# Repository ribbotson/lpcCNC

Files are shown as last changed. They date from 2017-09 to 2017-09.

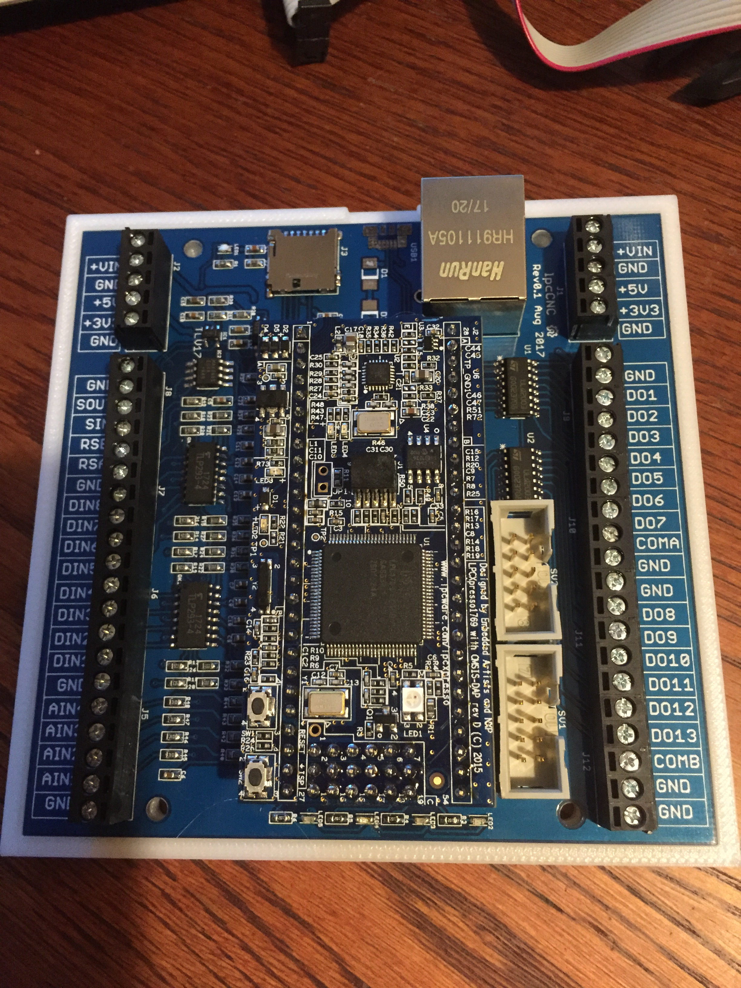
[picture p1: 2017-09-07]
document/IMG_2888.JPG

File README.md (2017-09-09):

# lpcCNC Smoothieboard Derivative for CNC applications

This free open source derivative of the Smoothieboard is designed for CNC applications. It is intended for use with external stepper motor drivers. It features 13 digital open collector outputs, 8 digital inputs, 4 analog inputs, RS485 interface for spindle, 10V analog output for spindle, support for LCD screen, Ethernet, and power supply up to 40V.

## Content

This is a hardware project with PCB design file in Eagle. A 3D printable case ([Top]( http://a360.co/2vPnznS), [Bottom](http://a360.co/2j534xu)) design in Fusion360 is also provided. Example configuration files for Smoothieware and grbl-lpc are also provided.

## Authors

* **Richard Ibbotson**  

## License

Licensed under CERN OHL v.1.2 or later https://www.ohwr.org/documents/294 No warranty is provided for this documentation implied or otherwise.

## Acknowledgments

* All the folks at [rLab](http://www.rlab.org.uk) Reading Hackspace especially Toby
+ The Smoothieboard creators and the [Smoothieware](http://smoothieware.org/) team

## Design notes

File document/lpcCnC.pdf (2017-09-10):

Lable | CPU Pin | Description
+VIN | N/A | External Power Supply input
GND | GND | System Ground
+5V | N/A | +5V Power Supply Output
+3V3 | N/A | +3V3 Power Supply Output
GND | GND | System Ground
SGND | N/A | Isolated Ground for Analog Spindle
SOUT | N/A | 0-> 10V Output for Analog Spindle
SIN | N/A | 10V supply in for Analog Spindle
RSB | N/A | - RS485 for Spindle
RSA | N/A | +RS485 for Spindle
GND | GND | System Ground
DIN8 | 2.13 | Digital Input
DIN7 | 1.31 | Digital Input
DIN6 | 1.29 | Digital Input
DIN5 | 1.28 | Digital Input
DIN4 | 1.26 | Digital Input
DIN3 | 1.25 | Digital Input
DIN2 | 1.24 | Digital Input
DIN1 | 1.23 | Digital Input
GND | GND | System Ground
AIN4 | 0.23 | Analog Input
AIN3 | 0.24 | Analog Input
AIN2 | 0.25 | Analog Input
AIN1 | 0.26 | Analog Input
GND | GND | System Ground

# lpcCNC Screw Terminal Mapping

Lable | CPU Pin | Description
+VIN | N/A | External Power Supply input
GND | GND | System Ground
+5V | N/A | +5V Power Supply Output
+3V3 | N/A | +3V3 Power Supply Output
GND | GND | System Ground
GND | GND | System Ground
DO1 | 0.4 | Digital Output
DO2 | 0.5 | Digital Output
DO3 | 0.10 | Digital Output
DO4 | 0.11 | Digital Output
DO5 | 2.0 | Digital Output
DO6 | 2.1 | Digital Output
DO7 | 2.2 | Digital Output
COMA | N/A | Protection Diode for DO1 to DO7
GND | GND | System Ground
GND | GND | System Ground
DO8 | 2.3 | Digital Output
DO9 | 2.4 | Digital Output
DO10 | 2.11 | Digital Output
DO11 | 2.8 | Digital Output
DO12 | 2.7 | Digital Output
DO13 | 2.6 | Digital Output
COMB | N/A | Protection Diode for DO8 to DO13
GND | GND | System Ground
GND | GND | System Ground

# lpcCNC CPU Pin Usage

Pin | Usage
0.0 | RS485 RX for Spindle
0.1 | RS485 TX for Spindle
0.2 | UART TX to LCD Panel and ISP AUX3 Pin 2
0.3 | UART RX to LCD Panel and ISP AUX3 Pin 1
0.4 | DO1 Digital Output
0.5 | DO2 Digital Output
0.6 | SSEL for Internal SD Card
0.7 | SCK for internal SD Card
0.8 | MISO for Internal SD Card
0.9 | MOSI for Internal SD Card
0.10 | DO3 Digital Output
0.11 | DO4 Digital Output
0.15 | SCK for LCD Panel AUX3 Pin 7
0.16 | SSEL for LCD Panel SD Card AUX3 Pin 8
0.17 | MOSI for LCD Panel AUX3 Pin6
0.18 | MISO for LCD Panel AUX3 Pin 5
0.19 | SDA Internal EEPROM
0.20 | SCL Internal EEPROM
0.21 | RS485 Direction for Spindle
0.22 | RED Diagnostic LED
0.23 | AN4 Analog Input
0.24 | AN3 Analog Input
0.25 | AN2 Analog Input
0.26 | AN1 Analog Input
0.27 | Not Used
0.28 | Not Used
0.29 | USB – Micro USB Connector
0.30 | USB + Micro USB Connector
Pin | Usage
1.0 | Ethernet
1.1 | Ethernet
1.4 | Ethernet
1.8 | Ethernet
1.9 | Ethernet
1.10 | Ethernet
1.14 | Ethernet
1.15 | Ethernet
1.16 | Ethernet
1.17 | Ethernet
1.18 | LED 2
1.19 | LED 3
1.20 | LED 4
1.21 | LED 5
1.22 | SSEL for LCD Panel LCD AUX2 Pin 3
1.23 | DIN1 Digital Input
1.24 | DIN2 Digital Input
1.25 | DIN3 Digital Input
1.26 | DIN4 Digital Input
1.27 | Encoder B for LC D Panel AUX 2 Pin 6
1.28 | DIN5 Digital Input
1.29 | DIN6 Digital Input
1.30 | Buzzer for LCD Panel AUX 2 Pin 2
1.31 | DIN7 Digital Input
Pin | Usage
2.0 | DO5 Digital Output
2.1 | DO6 Digital Output
2.2 | DO7 Digital Output
2.3 | DO8 Digital Output
2.4 | DO9 Digital Output
2.5 | PWM for Analog Spindle
2.6 | DO13 Digital Output
2.7 | DO12 Digital Output
2.8 | DO11 Digital Output
2.9 | USB Connect Internal
2.10 | ISP Enable Internal
2.11 | DO10 Digital Output
2.12 | A0 for LCD Panel AUX2 Pin 5
2.13 | DIN8 Digital Input
Pin | Usage
4.28 | Encoder Click for LCD Panel AUX2 Pin 1
4.29 | Encoder A for LCD Panel AUX2 Pin 8
Pin | Usage
3.25 | BLUE Diagnostic LED
3.26 | GREEN Diagnostic LED
Pin | Usage
Reset | Reset from LCD Panel AUX2 Pin 4

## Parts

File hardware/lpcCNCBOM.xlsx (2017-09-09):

Column1 | Column2 | Column3 | Column4 | Column5 | Column6 | Column7 | Column8 | Column9
Part | Value | Device | Package | Description | Manufacturer | Manufacturer Part Number | Supplier | Supplier Part number
AUX2 | 10 Way | Header | 10 Way | 10 Way Boxed Header | TruConnect | DS1013-10 | Rapid | 19-0033
AUX3 | 10 Way | Header | ML10 | 10 Way Boxed Header | TruConnect | DS1013-10 | Rapid | 19-0033
C1 | 100n | Cap Ceramic 50V | 0603 | Ceramic Capacitors | Murata | GRM188F51H104ZA01D | RS | 723-5534
C2 | 100n | Cap Ceramic 50V | 0603 | Ceramic Capacitors | Murata | GRM188F51H104ZA01D | RS | 723-5534
C3 | 100n | Cap Ceramic 50V | 0603 | Ceramic Capacitors | Murata | GRM188F51H104ZA01D | RS | 723-5534
C4 | 100n | Cap Ceramic 50V | 0603 | Ceramic Capacitors | Murata | GRM188F51H104ZA01D | RS | 723-5534
C5 | 100n | Cap Ceramic 50V | 0603 | Ceramic Capacitors | Murata | GRM188F51H104ZA01D | RS | 723-5534
C6 | 100n | Cap Ceramic 50V | 0603 | Ceramic Capacitors | Murata | GRM188F51H104ZA01D | RS | 723-5534
C7 | 100n | Cap Ceramic 50V | 0603 | Ceramic Capacitors | Murata | GRM188F51H104ZA01D | RS | 723-5534
C8 | 100n | Cap Ceramic 50V | 0603 | Ceramic Capacitors | Murata | GRM188F51H104ZA01D | RS | 723-5534
C9 | 100n | Cap Ceramic 50V | 0603 | Ceramic Capacitors | Murata | GRM188F51H104ZA01D | RS | 723-5534
C10 | 100n | Cap Ceramic 50V | 0603 | Ceramic Capacitors | Murata | GRM188F51H104ZA01D | RS | 723-5534
C11 | 100n | Cap Ceramic 50V | 0603 | Ceramic Capacitors | Murata | GRM188F51H104ZA01D | RS | 723-5534
C12 | 100n | Cap Ceramic 50V | 0603 | Ceramic Capacitors | Murata | GRM188F51H104ZA01D | RS | 723-5534
C13 | 100n | Cap Ceramic 50V | 0603 | Ceramic Capacitors | Murata | GRM188F51H104ZA01D | RS | 723-5534
C14 | 100n | Cap Ceramic 50V | 0603 | Ceramic Capacitors | Murata | GRM188F51H104ZA01D | RS | 723-5534
C15 | 47n | Cap Ceramic 50V | 0603 | Ceramic Capacitors | Murata | GRM188B11E473KA01D | RS | 798-0332
C16 | 1uF | Cap Ceramic 25V | 0603 | Ceramic Capacitors | Murata | GRM188R61E105KA12D | RS | 723-5587
C17 | 100n | Cap Ceramic 50V | 0603 | Ceramic Capacitors | Murata | GRM188F51H104ZA01D | RS | 723-5534
C18 | 100n | Cap Ceramic 50V | 0603 | Ceramic Capacitors | Murata | GRM188F51H104ZA01D | RS | 723-5534
C19 | 1uF | Cap Ceramic 25V | 0603 | Ceramic Capacitors | Murata | GRM188R61E105KA12D | RS | 723-5587
C20 | 1uF | Cap Ceramic 25V | 0603 | Ceramic Capacitors | Murata | GRM188R61E105KA12D | RS | 723-5587
C21 | 1uF | Cap Ceramic 25V | 0603 | Ceramic Capacitors | Murata | GRM188R61E105KA12D | RS | 723-5587
C22 | 1uF | Cap Ceramic 25V | 0603 | Ceramic Capacitors | Murata | GRM188R61E105KA12D | RS | 723-5587
C23 | 100n | Cap Ceramic 50V | 0603 | Ceramic Capacitors | Murata | GRM188F51H104ZA01D | RS | 723-5534
D1 | MBRA140 | DIODE-DO-214AC | DO-214AC | Schottky Power Diode | ON Semi | MBRA140T3G | RS | 625-5650
D2 | MBRA140 | DIODE-DO-214AC | DO-214AC | Schottky Power Diode | ON Semi | MBRA140T3G | RS | 625-5650
D3 | BAS70-04 | DIODE_2CACA-SOT23 | SOT23 | Dual Schottky Diode | Multicomp | BAS70-04 | Farnell | 179-7835
D4 | BAS70-04 | DIODE_2CACA-SOT23 | SOT23 | Dual Schottky Diode | Multicomp | BAS70-04 | Farnell | 179-7835
D5 | BAS70-04 | DIODE_2CACA-SOT23 | SOT23 | Dual Schottky Diode | Multicomp | BAS70-04 | Farnell | 179-7835
D6 | BAS70-04 | DIODE_2CACA-SOT23 | SOT23 | Dual Schottky Diode | Multicomp | BAS70-04 | Farnell | 179-7835
IC1 | TLV172 | TLV172MF | SOT23-5 | Low Power Single Op Amp | Texas Instruments | TLV172IDBVR | Farnell | 267-7088
IC2 | MAX3485 | MAX481CSA | SO08 | RS485 Transceiver | Maxim | MAX3485ECSA+ | Farnell | 251-8816
J1 | 1X5 | 1X5 | 1X05-3.5MM | 3.5mm Pitch Screw Header | CamdenBoss | CTB3051/5BK | Rapid | 21-4708
J2 | 1X5 | 1X5 | 1X05-3.5MM | 3.5mm Pitch Screw Header | CamdenBoss | CTB3051/5BK | Rapid | 21-4708
J3 |  | AMPHENOL_114-00841-68 | AMPHENOL_114-00841-68 | Micro SD Card Holder | Amphenol | 114-00841-68 | Farnell | 266-6772
J4 | HR911105A | HR911105A | HR911105A | Ethernet Mag Jack | HanRun | HR911105A | eBay | HR911105A
J5 | 1X5 | 1X5 | 1X05-3.5MM | 3.5mm Pitch Screw Header | CamdenBoss | CTB3051/5BK | Rapid | 21-4708
J6 | 1X5 | 1X5 | 1X05-3.5MM | 3.5mm Pitch Screw Header | CamdenBoss | CTB3051/5BK | Rapid | 21-4708
J7 | 1X5 | 1X5 | 1X05-3.5MM | 3.5mm Pitch Screw Header | CamdenBoss | CTB3051/5BK | Rapid | 21-4708
J8 | 1X5 | 1X5 | 1X05-3.5MM | 3.5mm Pitch Screw Header | CamdenBoss | CTB3051/5BK | Rapid | 21-4708
J9 | 1X5 | 1X5 | 1X05-3.5MM | 3.5mm Pitch Screw Header | CamdenBoss | CTB3051/5BK | Rapid | 21-4708
J10 | 1X5 | 1X5 | 1X05-3.5MM | 3.5mm Pitch Screw Header | CamdenBoss | CTB3051/5BK | Rapid | 21-4708
J11 | 1X5 | 1X5 | 1X05-3.5MM | 3.5mm Pitch Screw Header | CamdenBoss | CTB3051/5BK | Rapid | 21-4708
J12 | 1X5 | 1X5 | 1X05-3.5MM | 3.5mm Pitch Screw Header | CamdenBoss | CTB3051/5BK | Rapid | 21-4708
J13 | 27 pin | 2.54mm Pitch Female | Pin Header | Female Pin Header |  | 40 Pin strip | eBay
J14 | 27 pin | 2.54mm Pitch Female | Pin Header | Female Pin Header |  | 40 Pin strip | eBay
J15 | 4 pin | 2.54mm Pitch Female | Pin Header | Female Pin Header |  | 40 Pin strip | eBay
J16 | 3 pin | 2.54mm Pitch Female | Pin Header | Female Pin Header |  | 40 Pin strip | eBay
J17 | 3 pin | 2.54mm Pitch Female | Pin Header | Female Pin Header |  | 40 Pin strip | eBay
J18 | 3 pin | 2.54mm Pitch Female | Pin Header | Female Pin Header |  | 40 Pin strip | eBay
J19 | 27 pin | 2.54mm Pitch Male | Pin Header | Male Pin Header |  | 40 Pin strip | eBay
J20 | 27 pin | 2.54mm Pitch Male | Pin Header | Male Pin Header |  | 40 Pin strip | eBay
J21 | 4 pin | 2.54mm Pitch Male | Pin Header | Male Pin Header |  | 40 Pin strip | eBay
J22 | 3 pin | 2.54mm Pitch Male | Pin Header | Male Pin Header |  | 40 Pin strip | eBay
J23 | 3 pin | 2.54mm Pitch Male | Pin Header | Male Pin Header |  | 40 Pin strip | eBay
J24 | 3 pin | 2.54mm Pitch Male | Pin Header | Male Pin Header |  | 40 Pin strip | eBay
LED1 | Green |  | LED 0603 | SMT LED | Osram | LP L296-J2L2-25 | RS | 915-4768
LED2 | Green |  | LED 0603 | SMT LED | Osram | LP L296-J2L2-25 | RS | 915-4768
LED3 | Green |  | LED 0603 | SMT LED | Osram | LP L296-J2L2-25 | RS | 915-4768
LED4 | Green |  | LED 0603 | SMT LED | Osram | LP L296-J2L2-25 | RS | 915-4768
LED5 | Green |  | LED 0603 | SMT LED | Osram | LP L296-J2L2-25 | RS | 915-4768
LPC1 | LPC Expresso1769 | LPCXPRESSO_LPC1769 | Custom | Processor Module | NXP | OM13085UL | Farnell | 252-3091
OC1 | TLP293-4 | TLP293-4 | SOIC16 | Quad Optocoupler | Toshiba | TLP293-4 | Farnell | 252-4319
OC2 | TLP293-4 | TLP293-4 | SOIC16 | Quad Optocoupler | Toshiba | Toshiba | Farnell | 252-4319
OC3 | ACPL217-500E | ACPL217 | SOIC4 | Optocoupler | Avago | ACPL-217-500E | Rapid | 75-0230
R1 | 1K | RESISTOR0603 | 0603 | Resistors | Panasonic | ERJ3EKF1001V | RS | 873-9223
R2 | 100K | RESISTOR0603 | 0603 | Resistors | Panasonic | ERJU03F1003V | RS | 873-9220
R3 | 1K | RESISTOR0603 | 0603 | Resistors | Panasonic | ERJ3EKF1001V | RS | 873-9223
R4 | 1K | RESISTOR0603 | 0603 | Resistors | Panasonic | ERJ3EKF1001V | RS | 873-9223
R5 | 1K | RESISTOR0603 | 0603 | Resistors | Panasonic | ERJ3EKF1001V | RS | 873-9223
R6 | 1K | RESISTOR0603 | 0603 | Resistors | Panasonic | ERJ3EKF1001V | RS | 873-9223
R7 | Do Not Fit | RESISTOR0603 | 0603 | Resistors | Vishay | CRCW06030000Z0EB | RS | 678-9670
R8 | 0R | RESISTOR0603 | 0603 | Resistors | Vishay | CRCW06030000Z0EB | RS | 678-9670
R9 | Do Not Fit | RESISTOR0603 | 0603 | Resistors | Vishay | CRCW06030000Z0EB | RS | 678-9670
R10 | Do Not Fit | RESISTOR0603 | 0603 | Resistors | Vishay | CRCW06030000Z0EB | RS | 678-9670
R11 | 0R | RESISTOR0603 | 0603 | Resistors | Vishay | CRCW06030000Z0EB | RS | 678-9670
R12 | Do Not Fit | RESISTOR0603 | 0603 | Resistors | Vishay | CRCW06030000Z0EB | RS | 678-9670
R13 | 470R | RESISTOR0603 | 0603 | Resistors | Panasonic | ERJPA3F4700V | RS | 862-6966
R14 | 470R | RESISTOR0603 | 0603 | Resistors | Panasonic | ERJPA3F4700V | RS | 862-6966
R15 | 470R | RESISTOR0603 | 0603 | Resistors | Panasonic | ERJPA3F4700V | RS | 862-6966
R16 | 470R | RESISTOR0603 | 0603 | Resistors | Panasonic | ERJPA3F4700V | RS | 862-6966
R17 | 470R | RESISTOR0603 | 0603 | Resistors | Panasonic | ERJPA3F4700V | RS | 862-6966
R18 | 470R | RESISTOR0603 | 0603 | Resistors | Panasonic | ERJPA3F4700V | RS | 862-6966
R19 | 470R | RESISTOR0603 | 0603 | Resistors | Panasonic | ERJPA3F4700V | RS | 862-6966
R20 | 470R | RESISTOR0603 | 0603 | Resistors | Panasonic | ERJPA3F4700V | RS | 862-6966
R21 | 2K2 | RESISTOR0603 | 0603 | Resistors | Panasonic | ERJU03F2201V | RS | 213-2317
R22 | 2K2 | RESISTOR0603 | 0603 | Resistors | Panasonic | ERJU03F2201V | RS | 213-2317
R23 | 2K2 | RESISTOR0603 | 0603 | Resistors | Panasonic | ERJU03F2201V | RS | 213-2317
R24 | 2K2 | RESISTOR0603 | 0603 | Resistors | Panasonic | ERJU03F2201V | RS | 213-2317
R25 | 2K2 | RESISTOR0603 | 0603 | Resistors | Panasonic | ERJU03F2201V | RS | 213-2317
R26 | 2K2 | RESISTOR0603 | 0603 | Resistors | Panasonic | ERJU03F2201V | RS | 213-2317
R27 | 2K2 | RESISTOR0603 | 0603 | Resistors | Panasonic | ERJU03F2201V | RS | 213-2317
R28 | 2K2 | RESISTOR0603 | 0603 | Resistors | Panasonic | ERJU03F2201V | RS | 213-2317
R29 | 1K | RESISTOR0603 | 0603 | Resistors | Panasonic | ERJ3EKF1001V | RS | 873-9223
R30 | 1K | RESISTOR0603 | 0603 | Resistors | Panasonic | ERJ3EKF1001V | RS | 873-9223
R31 | 1K | RESISTOR0603 | 0603 | Resistors | Panasonic | ERJ3EKF1001V | RS | 873-9223
R32 | 1K | RESISTOR0603 | 0603 | Resistors | Panasonic | ERJ3EKF1001V | RS | 873-9223
R33 | 1K | RESISTOR0603 | 0603 | Resistors | Panasonic | ERJ3EKF1001V | RS | 873-9223
R34 | 1K | RESISTOR0603 | 0603 | Resistors | Panasonic | ERJ3EKF1001V | RS | 873-9223
R35 | 1K | RESISTOR0603 | 0603 | Resistors | Panasonic | ERJ3EKF1001V | RS | 873-9223
R36 | 1K | RESISTOR0603 | 0603 | Resistors | Panasonic | ERJ3EKF1001V | RS | 873-9223
R37 | 470R | RESISTOR0603 | 0603 | Resistors | Panasonic | ERJPA3F4700V | RS | 862-6966
R38 | 2K2 | RESISTOR0603 | 0603 | Resistors | Panasonic | ERJU03F2201V | RS | 213-2317
R39 | 47K | RESISTOR0603 | 0603 | Resistors | Panasonic | ERJU03F4702V | RS | 873-9490
R40 | 4K7 | RESISTOR0603 | 0603 | Resistors | Panasonic | ERJU03F4701V | RS | 873-9497
R41 | 100K | RESISTOR0603 | 0603 | Resistors | Panasonic | ERJU03F1003V | RS | 873-9220
R42 | 4K7 | RESISTOR0603 | 0603 | Resistors | Panasonic | ERJU03F4701V | RS | 873-9497
R43 | 4K7 | RESISTOR0603 | 0603 | Resistors | Panasonic | ERJU03F4701V | RS | 873-9497
R44 | 4K7 | RESISTOR0603 | 0603 | Resistors | Panasonic | ERJU03F4701V | RS | 873-9497
R45 | 10K | RESISTOR0603 | 0603 | Resistors | Panasonic | ERJU03F1002V | RS | 873-9226
R46 | 10K | RESISTOR0603 | 0603 | Resistors | Panasonic | ERJU03F1002V | RS | 873-9226
R47 | 10K | RESISTOR0603 | 0603 | Resistors | Panasonic | ERJU03F1002V | RS | 873-9226
R48 | 10K | RESISTOR0603 | 0603 | Resistors | Panasonic | ERJU03F1002V | RS | 873-9226
R49 | 120R | RESISTOR0603 | 0603 | Resistors | Panasonic | ERJU03F1200V | RS | 873-9254
U1 | ULQ2003 | ULQ2003 | SOIC16 | DARLINGTON TRANSISTOR ARRAYS | ST Micro | ULQ2003D1013TR | Farnell | 234-1742
U2 | ULQ2003 | ULQ2003 | SOIC16 | DARLINGTON TRANSISTOR ARRAYS | ST Micro | ULQ2003D1013TR | Farnell | 234-1742
USB1 | MOLEX-47346-0001 | MOLEX-47346-0001 | MOLEX-47364-0001 | Micro USB Connector SMT | Molex | 47364-001 | RS | 702-5475
VR1 | 78SR | 78SR | Custom | 5V Switching DC DC non isolated converter | Murata | OKI-78SR-5/1.5-W36H-C | RS | 796-2138
PCB |  |  | Custom | Printed Circuit Board 2 Layer | PCB | Github File | PCBWay | Github File
Case Lid |  |  | Custom | ABS 3D Print | 3D Printed | Github File | 3D Hubs | Github File
Case Base |  |  | Custom | ABS 3D Print | 3D Printed | Github File | 3D Hubs | Github File
SC1 | CSK Self tapping | 2.2mm * 13mm |  | Self Tapping Countersink screw |  |  | eBay
SC2 | CSK Self tapping | 2.2mm * 13mm |  | Self Tapping Countersink screw |  |  | eBay
SC3 | CSK Self tapping | 2.2mm * 13mm |  | Self Tapping Countersink screw |  |  | eBay
SC4 | CSK Self tapping | 2.2mm * 13mm |  | Self Tapping Countersink screw |  |  | eBay
SD1 | 4Gb Micro SD |  |  | Micro SD Card
LCD1 | LCD Panel |  |  | AZS MZ LCD Display inc cables |  |  | Aliexpress

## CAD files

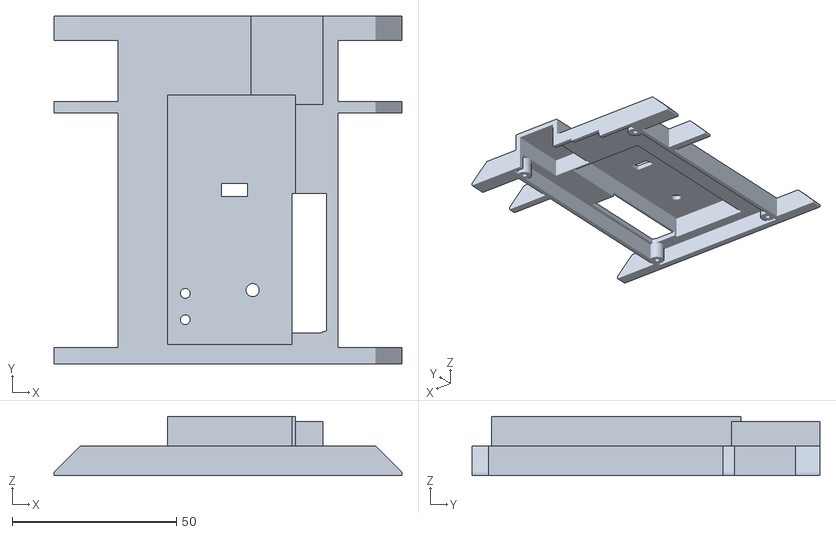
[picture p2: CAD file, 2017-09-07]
hardware/Case/STL/lpcCNC_Lid v15.stl
106.0 x 106.0 x 18.0

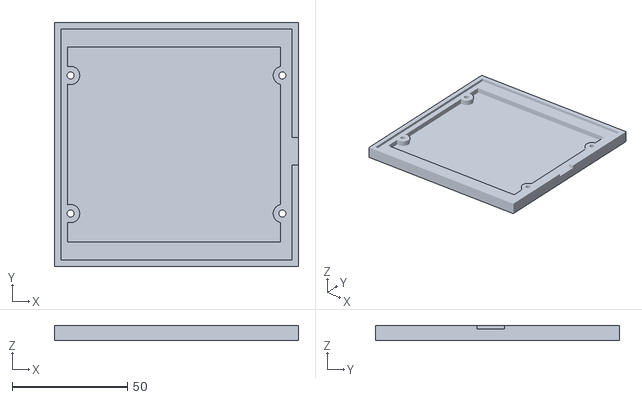
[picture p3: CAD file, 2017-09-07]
hardware/Case/STL/lpcCNC_Base v7.stl
106.0 x 106.0 x 6.60

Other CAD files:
hardware/Case/Fusion360/lpcCNC_Base v7.f3d
hardware/Case/Fusion360/lpcCNC_Lid v15.f3d

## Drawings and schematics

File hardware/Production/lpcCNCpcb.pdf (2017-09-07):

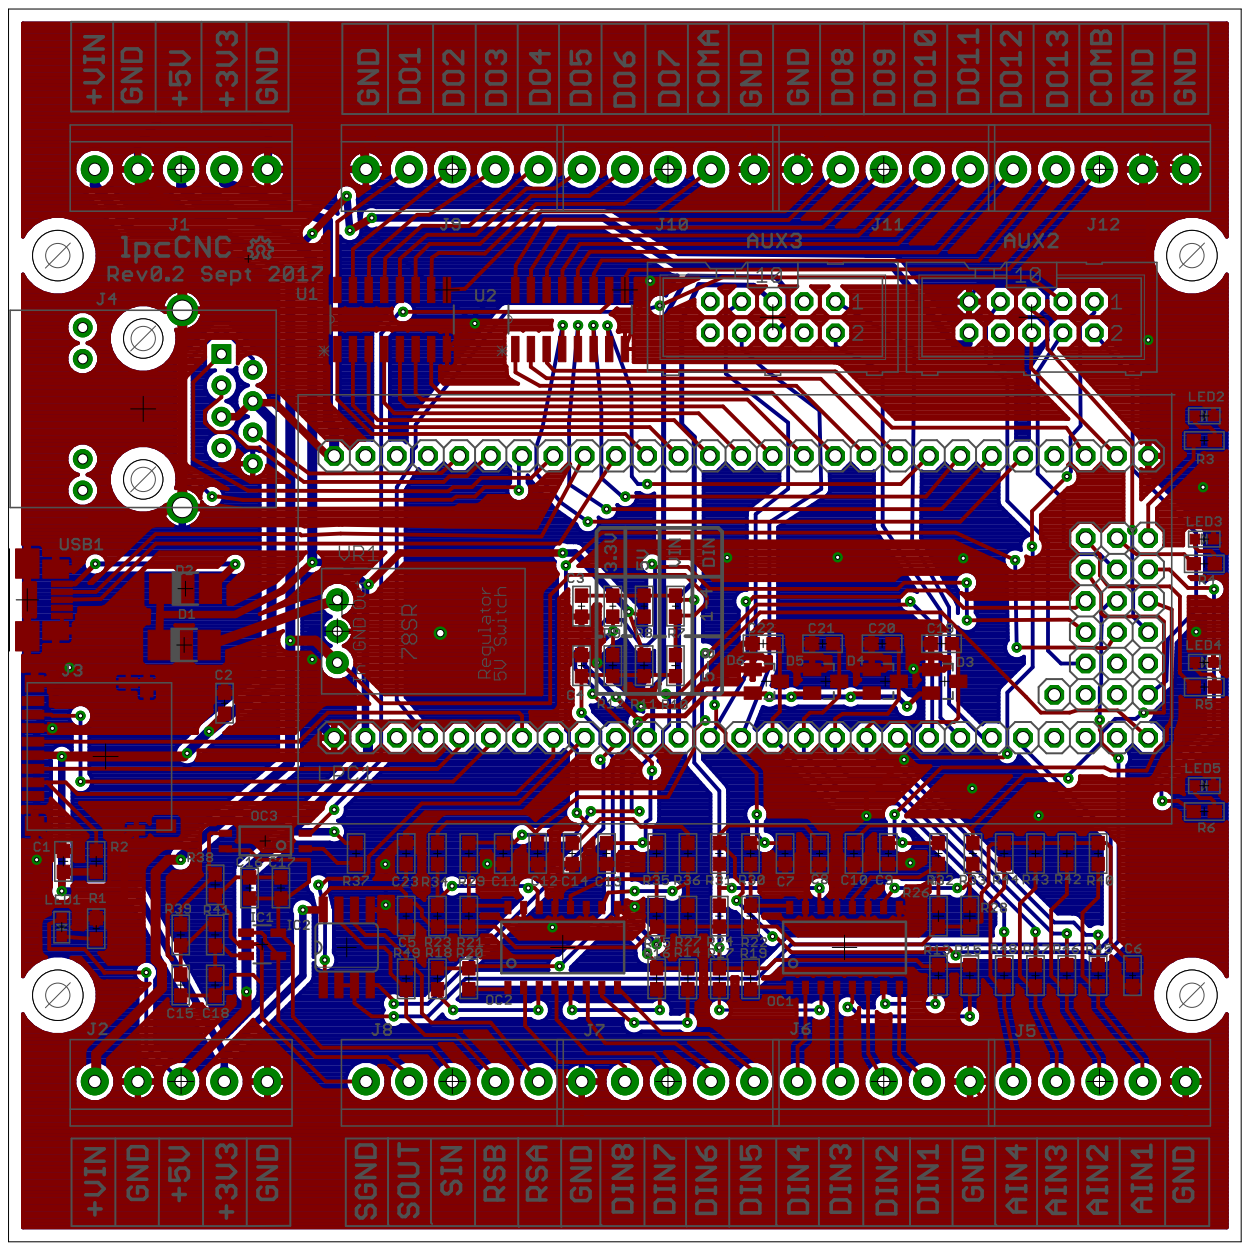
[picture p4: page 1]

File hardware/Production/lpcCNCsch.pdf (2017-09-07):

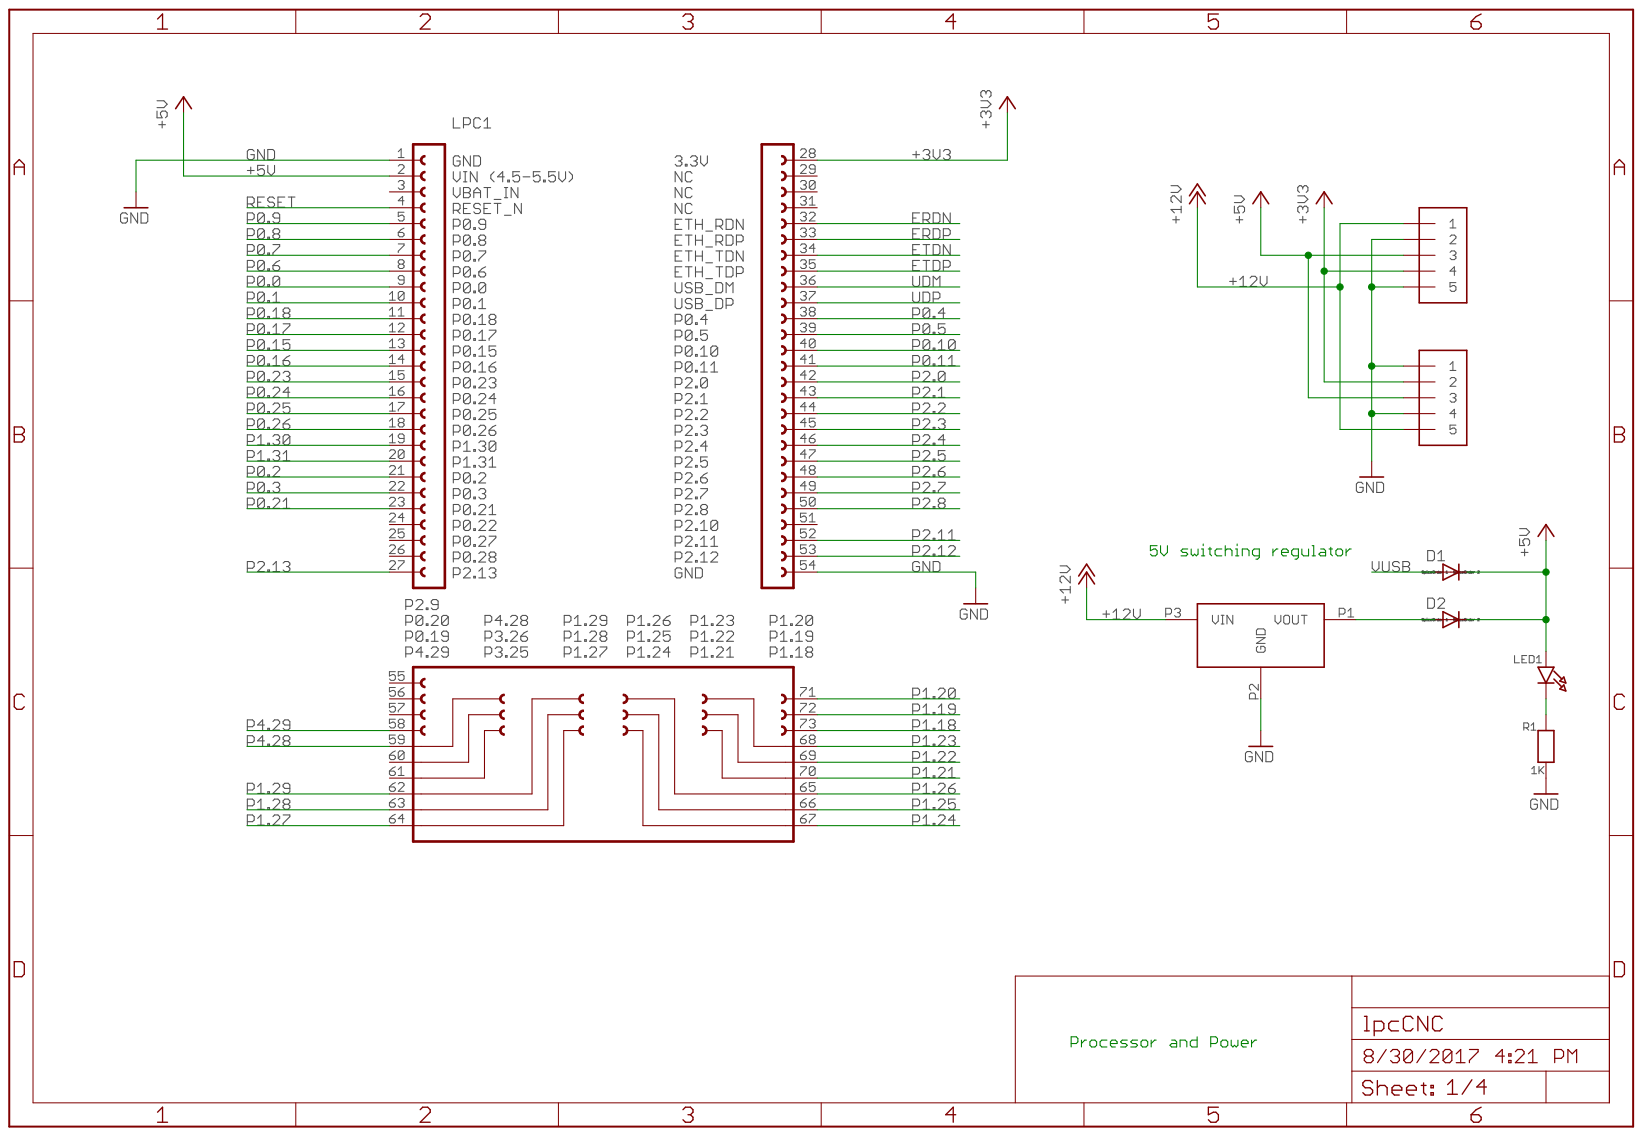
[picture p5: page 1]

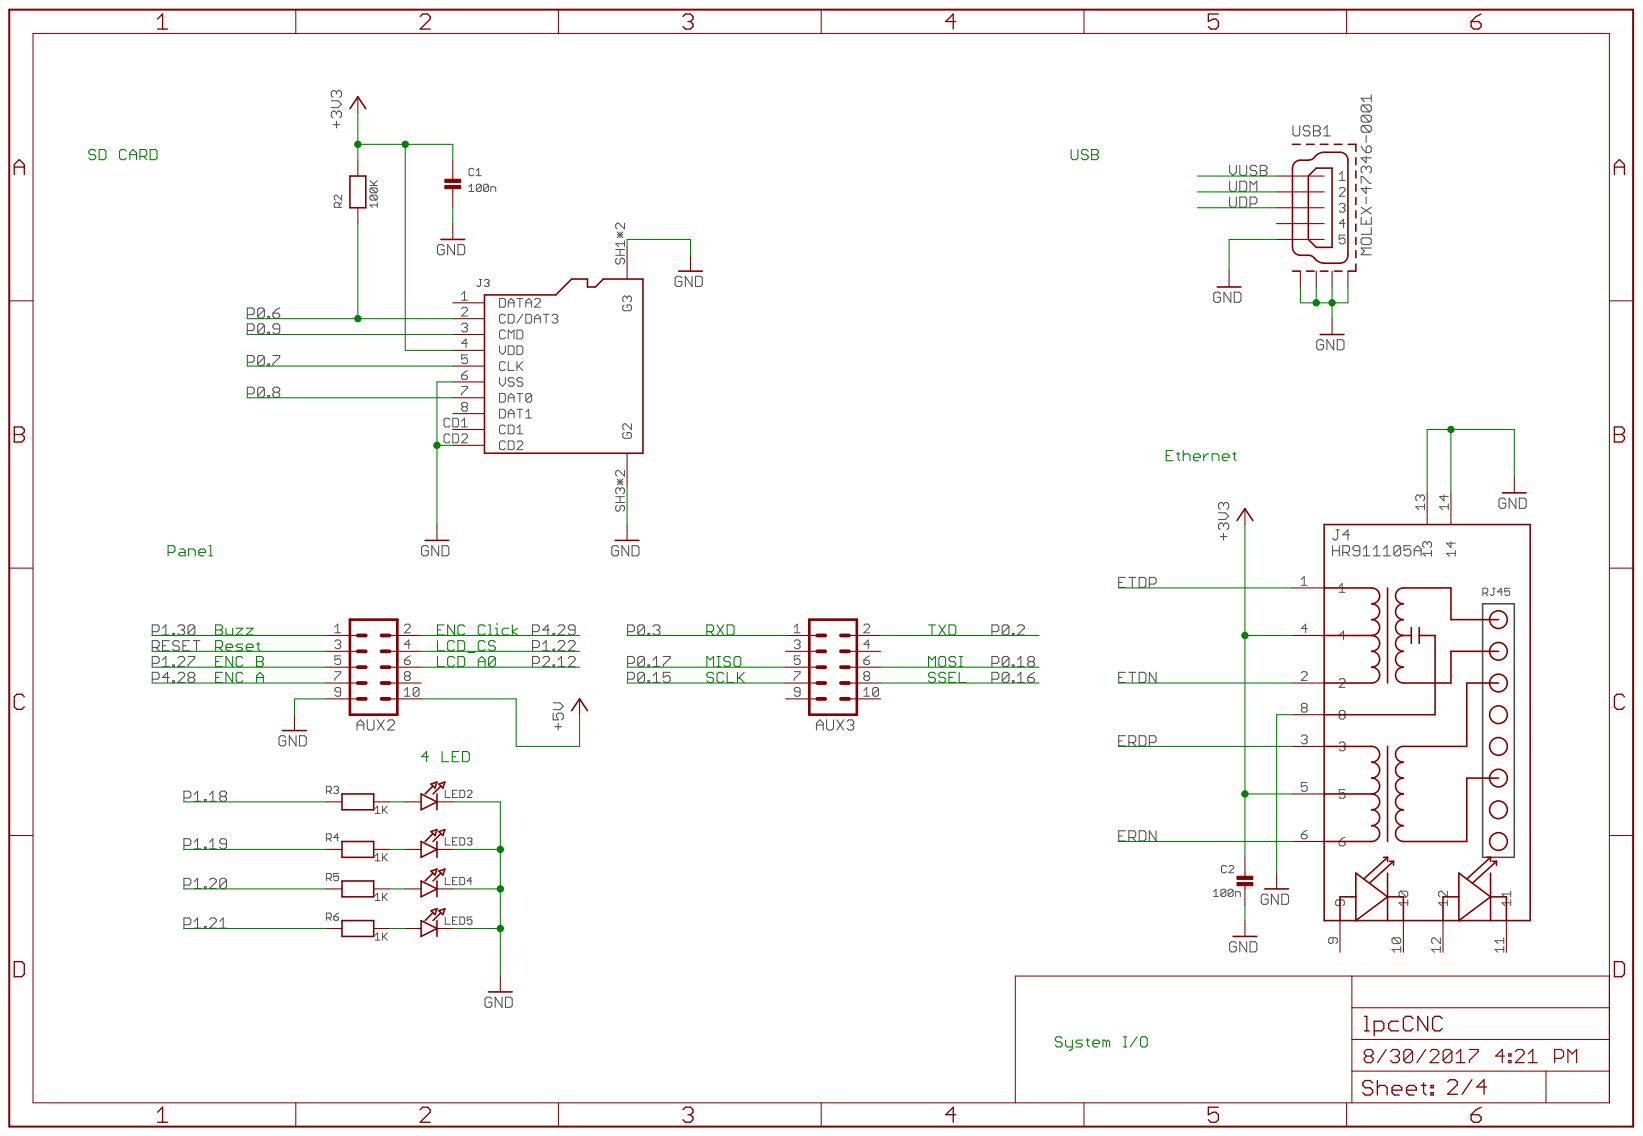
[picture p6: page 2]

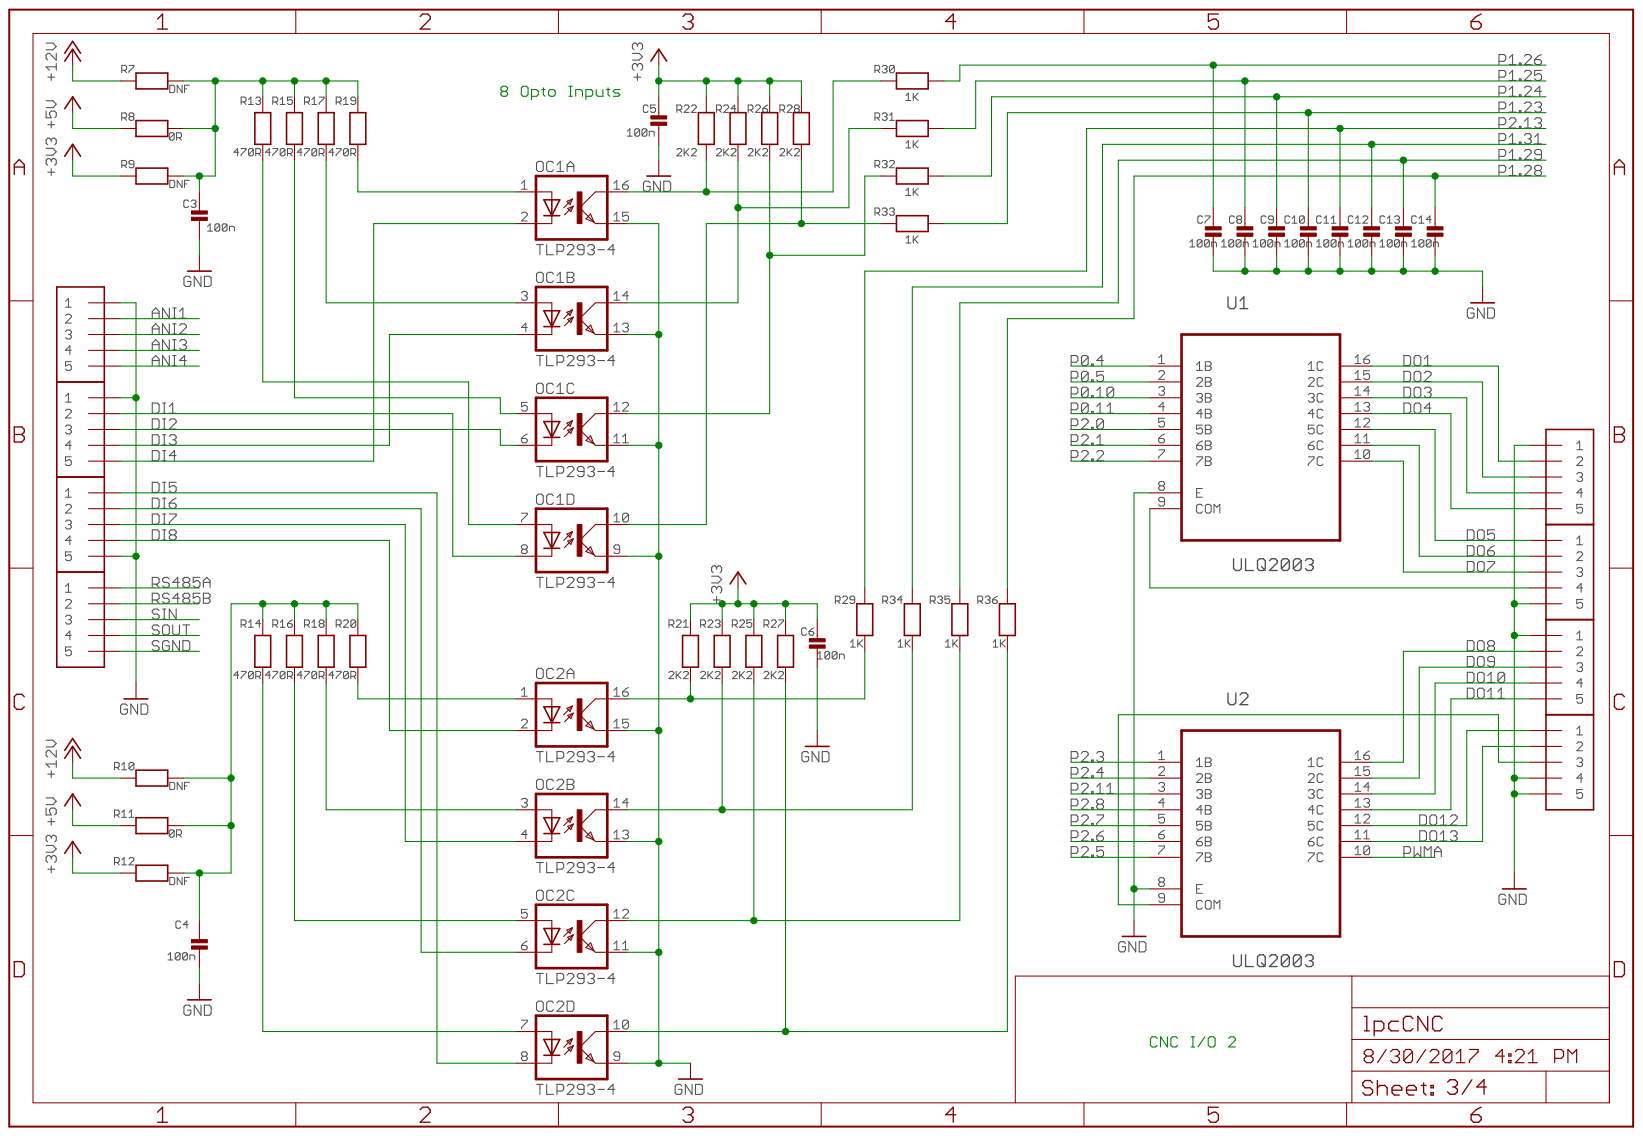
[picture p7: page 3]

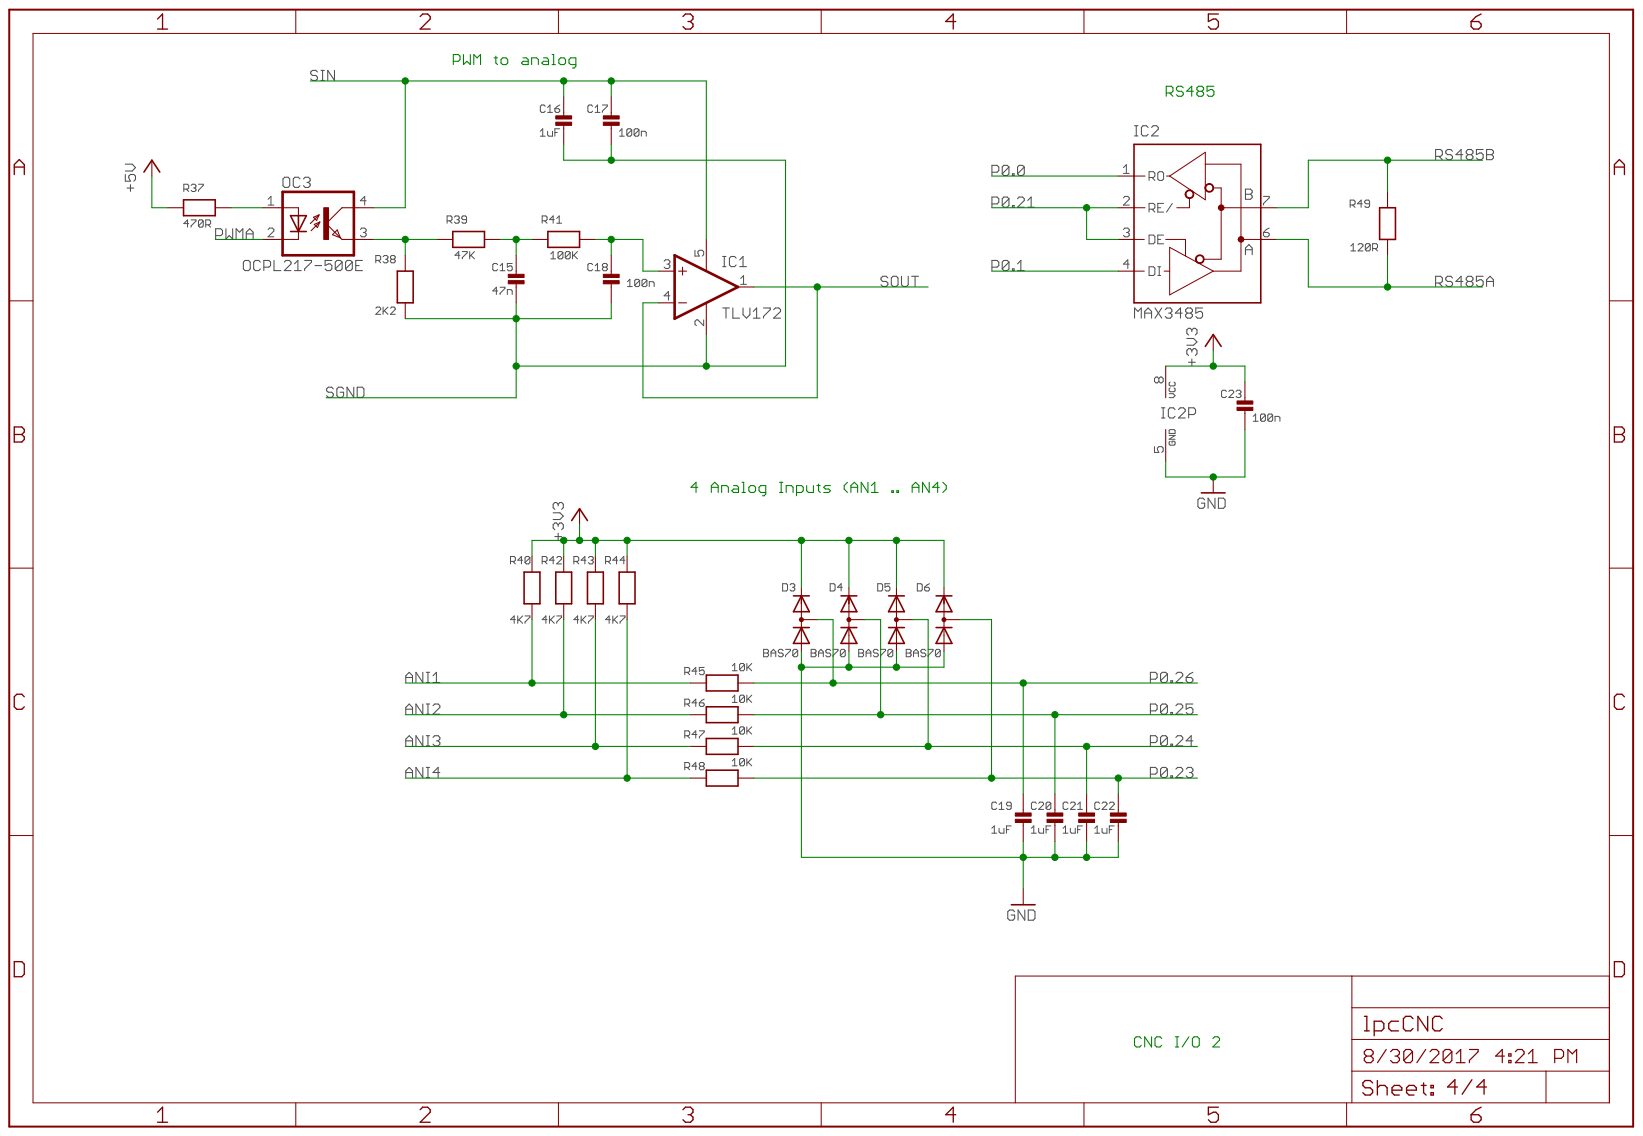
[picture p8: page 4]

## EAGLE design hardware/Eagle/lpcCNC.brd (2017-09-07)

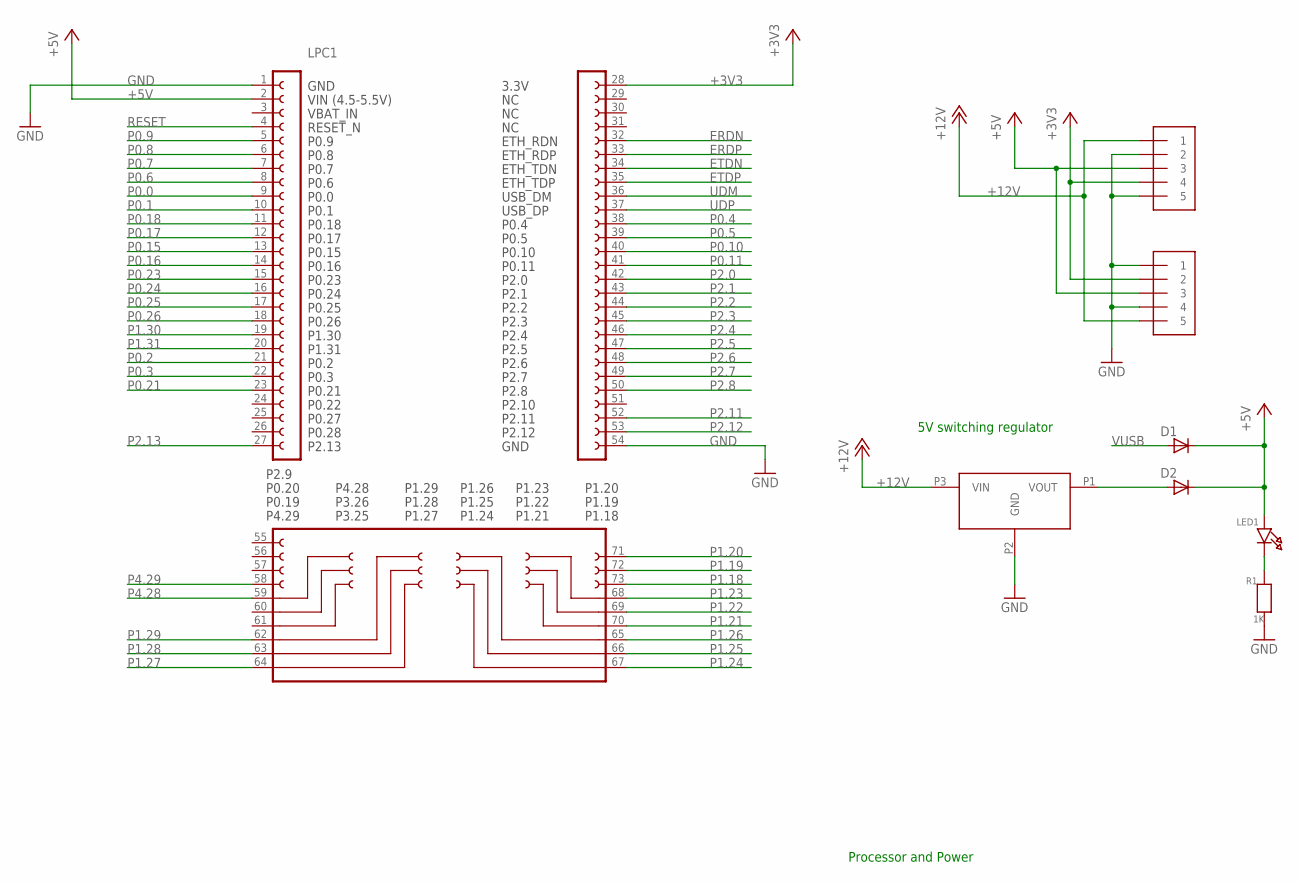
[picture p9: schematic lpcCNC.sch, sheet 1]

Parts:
D1, D2: DIODE-DO-214AC; DO-214AC
J1, J2: 1X5; 1X05-3.5MM
LED1: LED0603; CHIPLED_0603
LPC1: LPCXPRESSO_LPC1769
R1: 1K; 0603
VR1: 78SR

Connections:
+3V3: J1.4, J2.2, LPC1.28; also elsewhere on the board
+5V: D1.C, D2.C, J1.3, J2.3, LED1.A, LPC1.2; also elsewhere on the board
+12V: J1.1, J2.5, VR1.P3 (VIN); also elsewhere on the board
ERDN: LPC1.32; also elsewhere on the board
ERDP: LPC1.33; also elsewhere on the board
ETDN: LPC1.34; also elsewhere on the board
ETDP: LPC1.35; also elsewhere on the board
GND: J1.2, J1.5, J2.1, J2.4, LPC1.1, LPC1.54, R1.1, VR1.P2 (GND); also elsewhere on the board
unnamed: D2.A, VR1.P1 (VOUT)
unnamed: LED1.C, R1.2
P0.0: LPC1.9; also elsewhere on the board
P0.1: LPC1.10; also elsewhere on the board
P0.2: LPC1.21; also elsewhere on the board
P0.3: LPC1.22; also elsewhere on the board
P0.4: LPC1.38; also elsewhere on the board
P0.5: LPC1.39; also elsewhere on the board
P0.6: LPC1.8; also elsewhere on the board
P0.7: LPC1.7; also elsewhere on the board
P0.8: LPC1.6; also elsewhere on the board
P0.9: LPC1.5; also elsewhere on the board
P0.10: LPC1.40; also elsewhere on the board
P0.11: LPC1.41; also elsewhere on the board
P0.15: LPC1.13; also elsewhere on the board
P0.16: LPC1.14; also elsewhere on the board
P0.17: LPC1.12; also elsewhere on the board
P0.18: LPC1.11; also elsewhere on the board
P0.21: LPC1.23; also elsewhere on the board
P0.23: LPC1.15; also elsewhere on the board
P0.24: LPC1.16; also elsewhere on the board
P0.25: LPC1.17; also elsewhere on the board
P0.26: LPC1.18; also elsewhere on the board
P1.18: LPC1.73; also elsewhere on the board
P1.19: LPC1.72; also elsewhere on the board
P1.20: LPC1.71; also elsewhere on the board
P1.21: LPC1.70; also elsewhere on the board
P1.22: LPC1.69; also elsewhere on the board
P1.23: LPC1.68; also elsewhere on the board
P1.24: LPC1.67; also elsewhere on the board
P1.25: LPC1.66; also elsewhere on the board
P1.26: LPC1.65; also elsewhere on the board
P1.27: LPC1.64; also elsewhere on the board
P1.28: LPC1.63; also elsewhere on the board
P1.29: LPC1.62; also elsewhere on the board
P1.30: LPC1.19; also elsewhere on the board
P1.31: LPC1.20; also elsewhere on the board
P2.0: LPC1.42; also elsewhere on the board
P2.1: LPC1.43; also elsewhere on the board
P2.2: LPC1.44; also elsewhere on the board
P2.3: LPC1.45; also elsewhere on the board
P2.4: LPC1.46; also elsewhere on the board
P2.5: LPC1.47; also elsewhere on the board
P2.6: LPC1.48; also elsewhere on the board
P2.7: LPC1.49; also elsewhere on the board
P2.8: LPC1.50; also elsewhere on the board
P2.11: LPC1.52; also elsewhere on the board
P2.12: LPC1.53; also elsewhere on the board
P2.13: LPC1.27; also elsewhere on the board
P4.28: LPC1.59; also elsewhere on the board
P4.29: LPC1.58; also elsewhere on the board
RESET: LPC1.4; also elsewhere on the board
UDM: LPC1.36; also elsewhere on the board
UDP: LPC1.37; also elsewhere on the board
VUSB: D1.A; also elsewhere on the board

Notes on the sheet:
Processor and Power
5V switching regulator

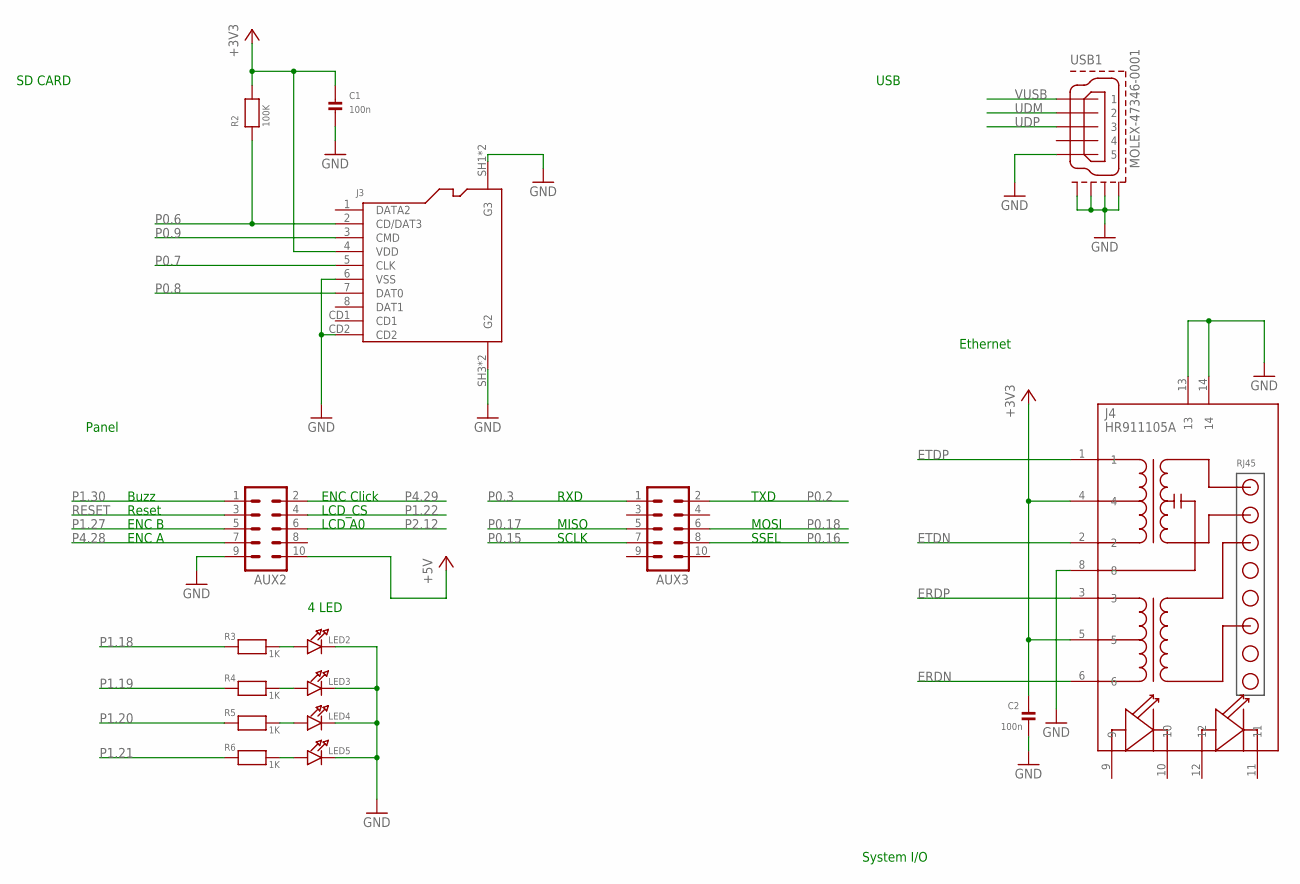
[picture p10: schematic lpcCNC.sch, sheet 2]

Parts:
AUX2, AUX3: ML10
C1, C2: 100n; 0603
J3: AMPHENOL_114-00841-68
J4: HR911105A
LED2, LED3, LED4, LED5: LED0603; CHIPLED_0603
R2: 100K; 0603
R3, R4, R5, R6: 1K; 0603
USB1: MOLEX-47346-0001; MOLEX-47364-0001

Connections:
+3V3: C1.1, C2.1, J3.4 (VDD), J4.4, J4.5, R2.2; also elsewhere on the board
+5V: AUX2.10; also elsewhere on the board
ERDN: J4.6; also elsewhere on the board
ERDP: J4.3; also elsewhere on the board
ETDN: J4.2; also elsewhere on the board
ETDP: J4.1; also elsewhere on the board
GND: AUX2.9, C1.2, C2.2, J3.6 (VSS), J3.CD2, J3.SH1 (G3), J3.SH2 (G3), J3.SH3 (G2), J3.SH4 (G2), J4.8, J4.13, J4.14, LED2.C, LED3.C, LED4.C, LED5.C, USB1.5, USB1.GND1, USB1.GND2, USB1.GND3, USB1.GND4; also elsewhere on the board
unnamed: LED2.A, R3.2
unnamed: LED3.A, R4.2
unnamed: LED4.A, R5.2
unnamed: LED5.A, R6.2
P0.2: AUX3.2; also elsewhere on the board
P0.3: AUX3.1; also elsewhere on the board
P0.6: J3.2 (CD/DAT3), R2.1; also elsewhere on the board
P0.7: J3.5 (CLK); also elsewhere on the board
P0.8: J3.7 (DAT0); also elsewhere on the board
P0.9: J3.3 (CMD); also elsewhere on the board
P0.15: AUX3.7; also elsewhere on the board
P0.16: AUX3.8; also elsewhere on the board
P0.17: AUX3.5; also elsewhere on the board
P0.18: AUX3.6; also elsewhere on the board
P1.18: R3.1; also elsewhere on the board
P1.19: R4.1; also elsewhere on the board
P1.20: R5.1; also elsewhere on the board
P1.21: R6.1; also elsewhere on the board
P1.22: AUX2.4; also elsewhere on the board
P1.27: AUX2.5; also elsewhere on the board
P1.30: AUX2.1; also elsewhere on the board
P2.12: AUX2.6; also elsewhere on the board
P4.28: AUX2.7; also elsewhere on the board
P4.29: AUX2.2; also elsewhere on the board
RESET: AUX2.3; also elsewhere on the board
UDM: USB1.2; also elsewhere on the board
UDP: USB1.3; also elsewhere on the board
VUSB: USB1.1; also elsewhere on the board

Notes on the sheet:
System I/O
Ethernet
USB
SD CARD
Panel
4 LED
ENC Click
LCD_CS
LCD A0
Reset
ENC A
ENC B
Buzz
TXD
RXD
MISO
SCLK
MOSI
SSEL

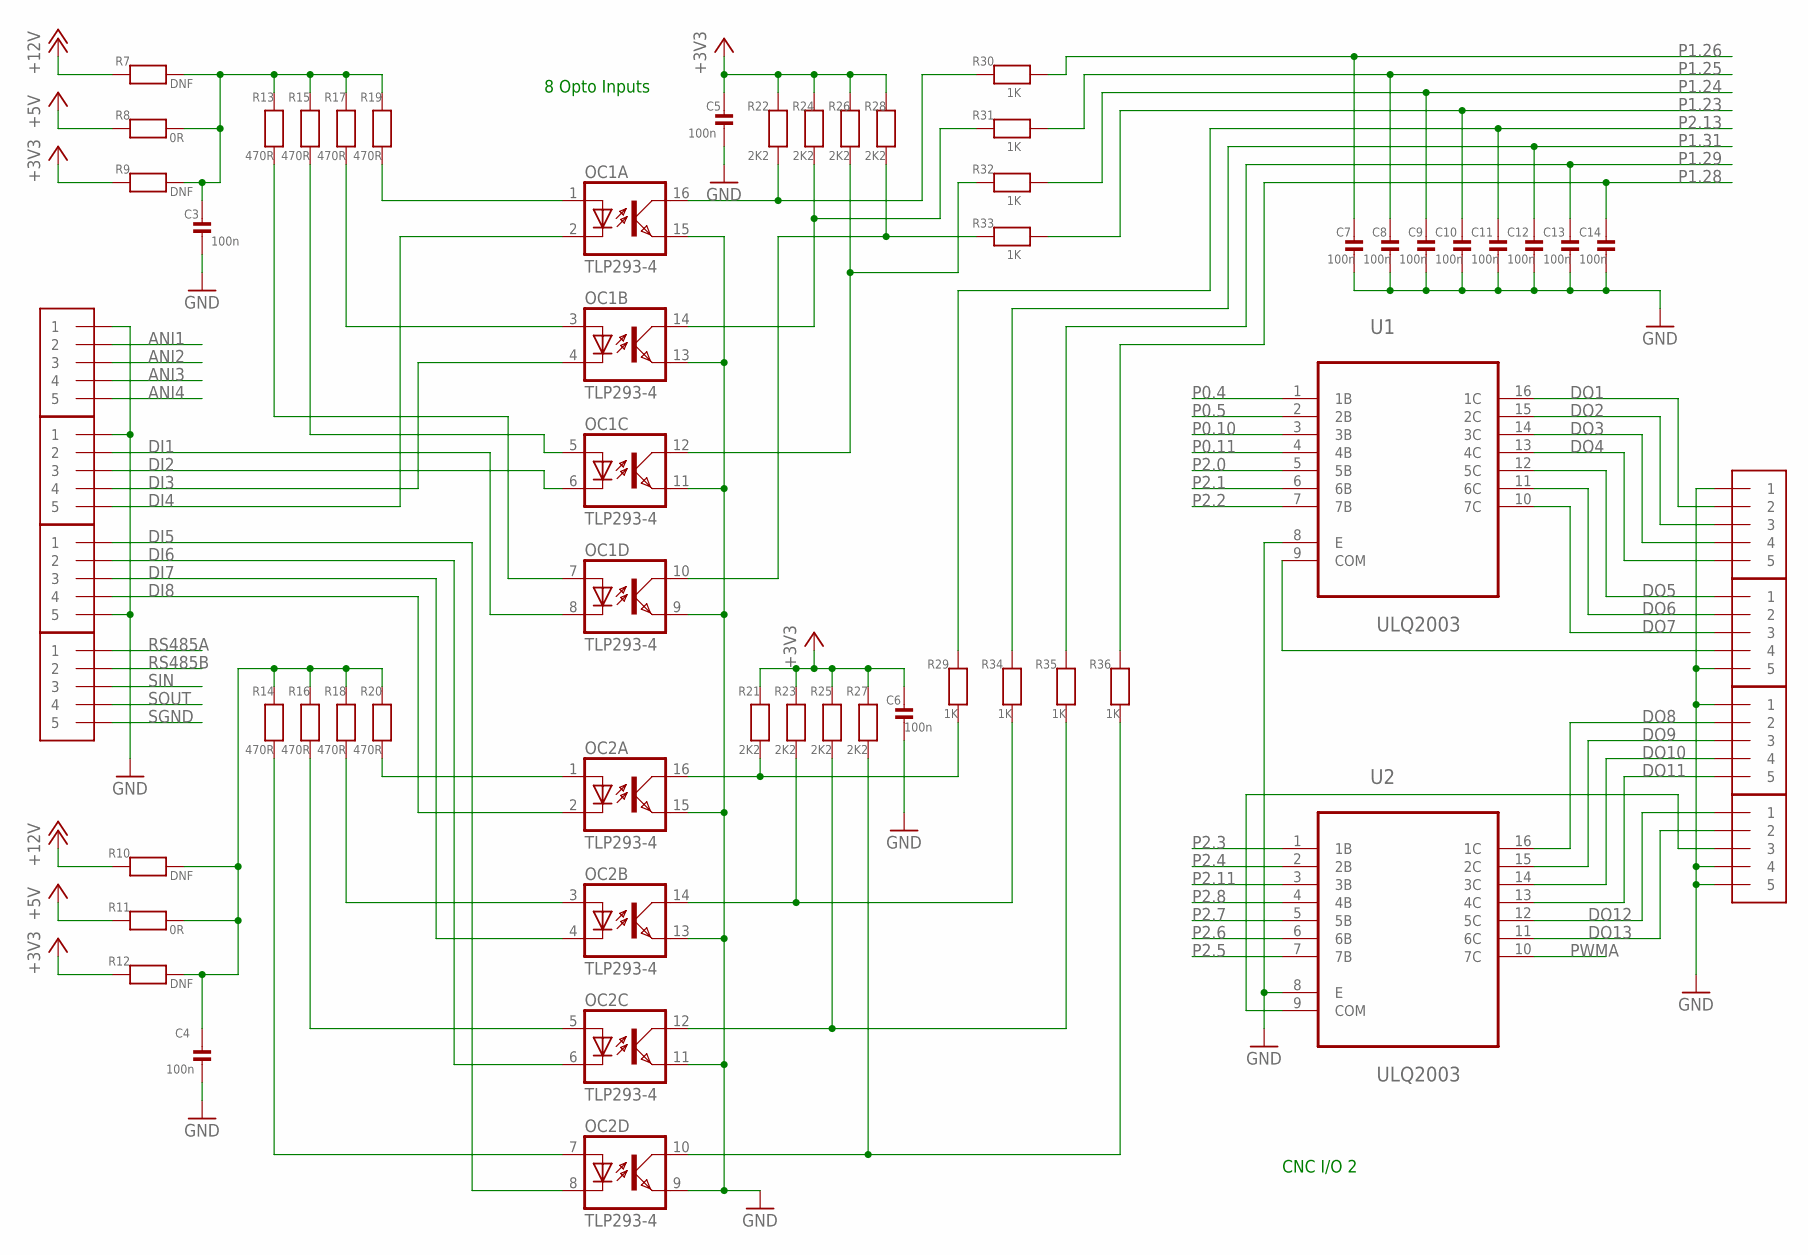
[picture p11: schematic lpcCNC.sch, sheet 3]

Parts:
C3, C4, C5, C6, C7, C8, C9, C10, C11, C12, C13, C14: 100n; 0603
J5, J6, J7, J8, J9, J10, J11, J12: 1X5; 1X05-3.5MM
OC1, OC2: TLP293-4; MINI-FLAT-16
R7, R9, R10, R12: DNF; 0603
R8, R11: 0R; 0603
R13, R14, R15, R16, R17, R18, R19, R20: 470R; 0603
R21, R22, R23, R24, R25, R26, R27, R28: 2K2; 0603
R29, R30, R31, R32, R33, R34, R35, R36: 1K; 0603
U1, U2: ULQ2003; SOIC127P600X175-16N

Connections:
+3V3: C5.1, C6.1, R9.2, R12.2, R21.2, R22.2, R23.2, R24.2, R25.2, R26.2, R27.2, R28.2; also elsewhere on the board
+5V: R8.2, R11.2; also elsewhere on the board
+12V: R7.2, R10.2; also elsewhere on the board
ANI1: J5.2; also elsewhere on the board
ANI2: J5.3; also elsewhere on the board
ANI3: J5.4; also elsewhere on the board
ANI4: J5.5; also elsewhere on the board
DI1: J6.2, OC1.8 (C)
DI2: J6.3, OC1.6 (C)
DI3: J6.4, OC1.4 (C)
DI4: J6.5, OC1.2 (C)
DI5: J7.1, OC2.8 (C)
DI6: J7.2, OC2.6 (C)
DI7: J7.3, OC2.4 (C)
DI8: J7.4, OC2.2 (C)
DO1: J9.2, U1.16 (1C)
DO2: J9.3, U1.15 (2C)
DO3: J9.4, U1.14 (3C)
DO4: J9.5, U1.13 (4C)
DO5: J10.1, U1.12 (5C)
DO6: J10.2, U1.11 (6C)
DO7: J10.3, U1.10 (7C)
DO8: J11.2, U2.16 (1C)
DO9: J11.3, U2.15 (2C)
DO10: J11.4, U2.14 (3C)
DO11: J11.5, U2.13 (4C)
DO12: J12.1, U2.12 (5C)
DO13: J12.2, U2.11 (6C)
GND: C3.2, C4.2, C5.2, C6.2, C7.2, C8.2, C9.2, C10.2, C11.2, C12.2, C13.2, C14.2, J5.1, J6.1, J7.5, J9.1, J10.5, J11.1, J12.4, J12.5, OC1.9 (EMIT), OC1.11 (EMIT), OC1.13 (EMIT), OC1.15 (EMIT), OC2.9 (EMIT), OC2.11 (EMIT), OC2.13 (EMIT), OC2.15 (EMIT), U1.8 (E), U2.8 (E); also elsewhere on the board
unnamed: J10.4, U1.9 (COM)
unnamed: J12.3, U2.9 (COM)
unnamed: C3.1, R7.1, R8.1, R9.1, R13.2, R15.2, R17.2, R19.2
unnamed: OC2.1 (A), R20.1
unnamed: OC2.3 (A), R18.1
unnamed: OC2.5 (A), R16.1
unnamed: OC2.7 (A), R14.1
unnamed: C4.1, R10.1, R11.1, R12.1, R14.2, R16.2, R18.2, R20.2
unnamed: OC1.1 (A), R19.1
unnamed: OC1.3 (A), R17.1
unnamed: OC1.5 (A), R15.1
unnamed: OC1.7 (A), R13.1
unnamed: OC1.16 (COL), R22.1, R30.2
unnamed: OC1.14 (COL), R24.1, R31.2
unnamed: OC2.16 (COL), R21.1, R29.1
unnamed: OC2.14 (COL), R23.1, R34.1
unnamed: OC2.12 (COL), R25.1, R35.1
unnamed: OC2.10 (COL), R27.1, R36.1
unnamed: OC1.12 (COL), R26.1, R32.2
unnamed: OC1.10 (COL), R28.1, R33.2
P0.4: U1.1 (1B); also elsewhere on the board
P0.5: U1.2 (2B); also elsewhere on the board
P0.10: U1.3 (3B); also elsewhere on the board
P0.11: U1.4 (4B); also elsewhere on the board
P1.23: C10.1, R33.1; also elsewhere on the board
P1.24: C9.1, R32.1; also elsewhere on the board
P1.25: C8.1, R31.1; also elsewhere on the board
P1.26: C7.1, R30.1; also elsewhere on the board
P1.28: C14.1, R36.2; also elsewhere on the board
P1.29: C13.1, R35.2; also elsewhere on the board
P1.31: C12.1, R34.2; also elsewhere on the board
P2.0: U1.5 (5B); also elsewhere on the board
P2.1: U1.6 (6B); also elsewhere on the board
P2.2: U1.7 (7B); also elsewhere on the board
P2.3: U2.1 (1B); also elsewhere on the board
P2.4: U2.2 (2B); also elsewhere on the board
P2.5: U2.7 (7B); also elsewhere on the board
P2.6: U2.6 (6B); also elsewhere on the board
P2.7: U2.5 (5B); also elsewhere on the board
P2.8: U2.4 (4B); also elsewhere on the board
P2.11: U2.3 (3B); also elsewhere on the board
P2.13: C11.1, R29.2; also elsewhere on the board
PWMA: U2.10 (7C); also elsewhere on the board
RS485A: J8.1; also elsewhere on the board
RS485B: J8.2; also elsewhere on the board
SGND: J8.5; also elsewhere on the board
SIN: J8.3; also elsewhere on the board
SOUT: J8.4; also elsewhere on the board

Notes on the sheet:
CNC I/O 2
8 Opto Inputs

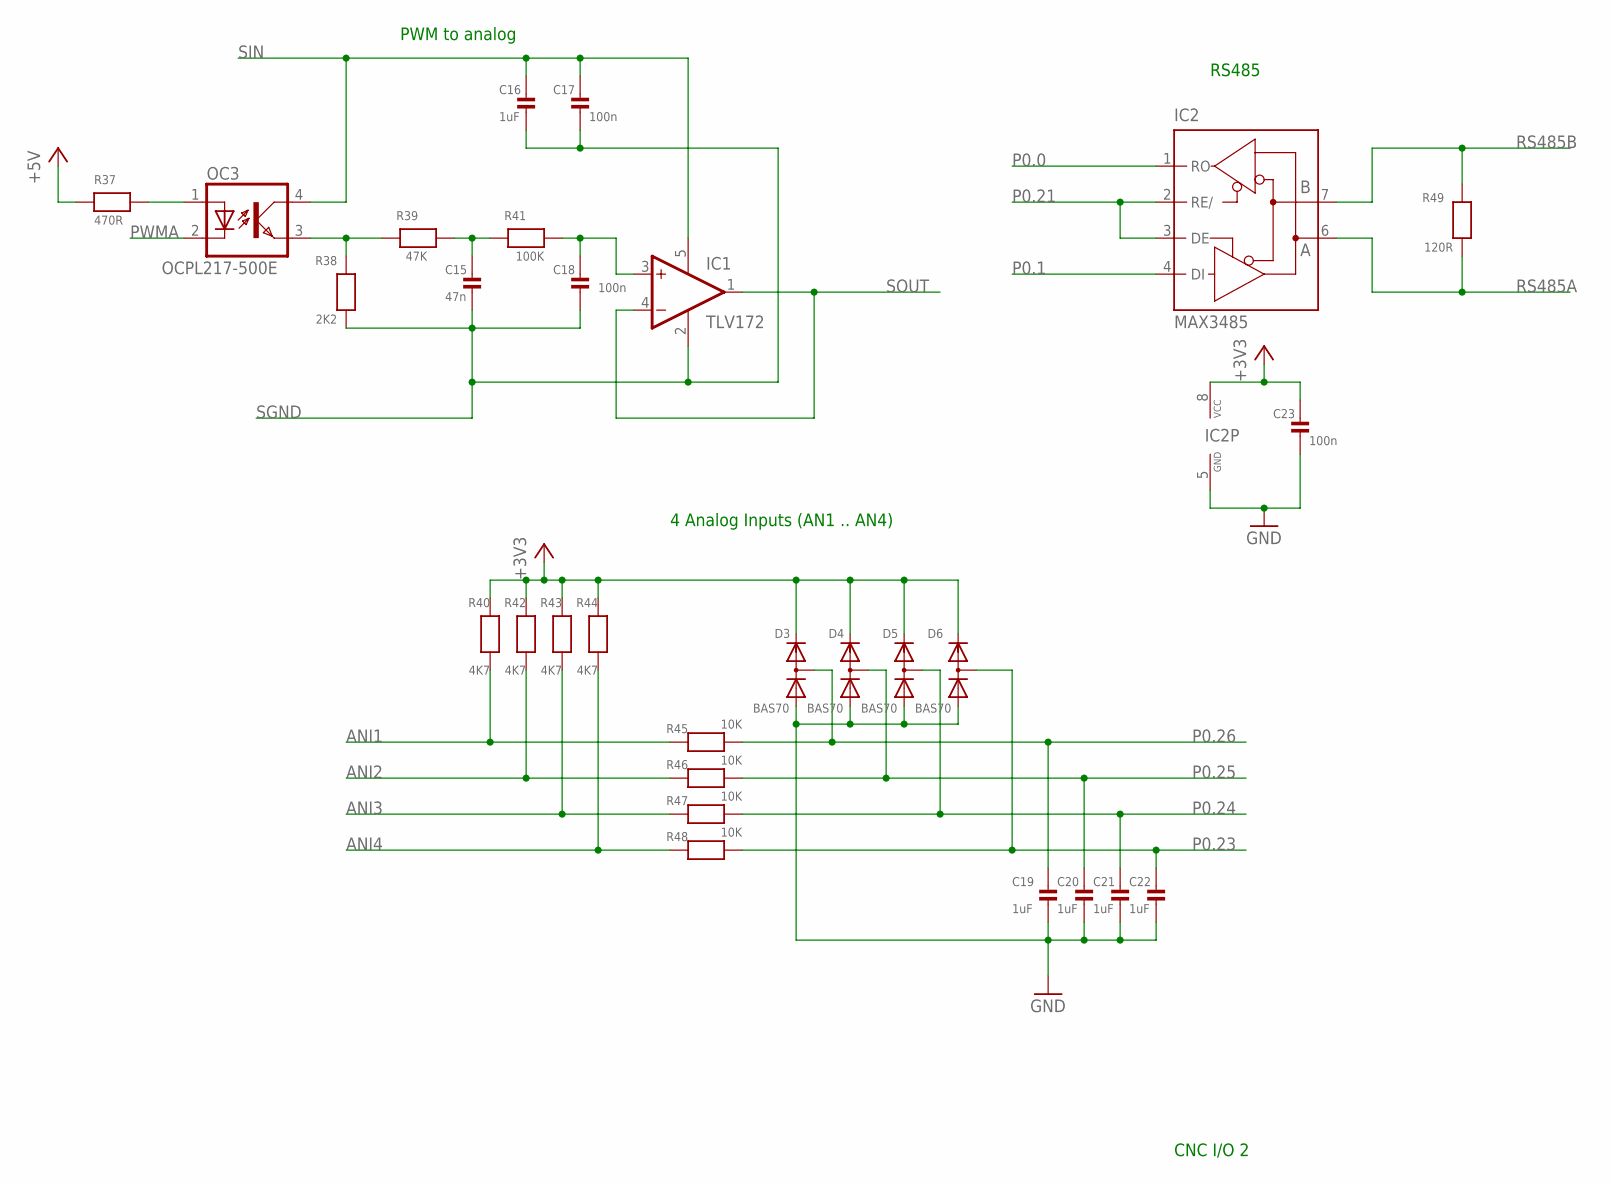
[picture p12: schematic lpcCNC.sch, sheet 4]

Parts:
C15: 47n; 0603
C16, C19, C20, C21, C22: 1uF; 0603
C17, C18, C23: 100n; 0603
D3, D4, D5, D6: BAS70; SOT23
IC1: TLV172; SOT23-5
IC2: MAX3485; SO08
OC3: OCPL217-500E; MINI-FLAT-4
R37: 470R; 0603
R38: 2K2; 0603
R39: 47K; 0603
R40, R42, R43, R44: 4K7; 0603
R41: 100K; 0603
R45, R46, R47, R48: 10K; 0603
R49: 120R; 0603

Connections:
+3V3: C23.1, D3.2 (C), D4.2 (C), D5.2 (C), D6.2 (C), IC2.8 (VCC), R40.2, R42.2, R43.2, R44.2; also elsewhere on the board
+5V: R37.1; also elsewhere on the board
ANI1: R40.1, R45.2; also elsewhere on the board
ANI2: R42.1, R46.2; also elsewhere on the board
ANI3: R43.1, R47.2; also elsewhere on the board
ANI4: R44.1, R48.2; also elsewhere on the board
GND: C19.2, C20.2, C21.2, C22.2, C23.2, D3.1 (A), D4.1 (A), D5.1 (A), D6.1 (A), IC2.5 (GND); also elsewhere on the board
unnamed: OC3.1 (A), R37.2
unnamed: OC3.3 (EMIT), R38.2, R39.2
unnamed: C15.1, R39.1, R41.2
unnamed: C18.1, IC1.3 (+IN), R41.1
P0.0: IC2.1 (RO); also elsewhere on the board
P0.1: IC2.4 (DI); also elsewhere on the board
P0.21: IC2.2 (RE/), IC2.3 (DE); also elsewhere on the board
P0.23: C22.1, D6.3 (AC), R48.1; also elsewhere on the board
P0.24: C21.1, D5.3 (AC), R47.1; also elsewhere on the board
P0.25: C20.1, D4.3 (AC), R46.1; also elsewhere on the board
P0.26: C19.1, D3.3 (AC), R45.1; also elsewhere on the board
PWMA: OC3.2 (C); also elsewhere on the board
RS485A: IC2.6 (A), R49.1; also elsewhere on the board
RS485B: IC2.7 (B), R49.2; also elsewhere on the board
SGND: C15.2, C16.2, C17.2, C18.2, IC1.2 (V-), R38.1; also elsewhere on the board
SIN: C16.1, C17.1, IC1.5 (V+), OC3.4 (COL); also elsewhere on the board
SOUT: IC1.1 (OUT), IC1.4 (-IN); also elsewhere on the board

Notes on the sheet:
CNC I/O 2
4 Analog Inputs (AN1 .. AN4)
PWM to analog
RS485

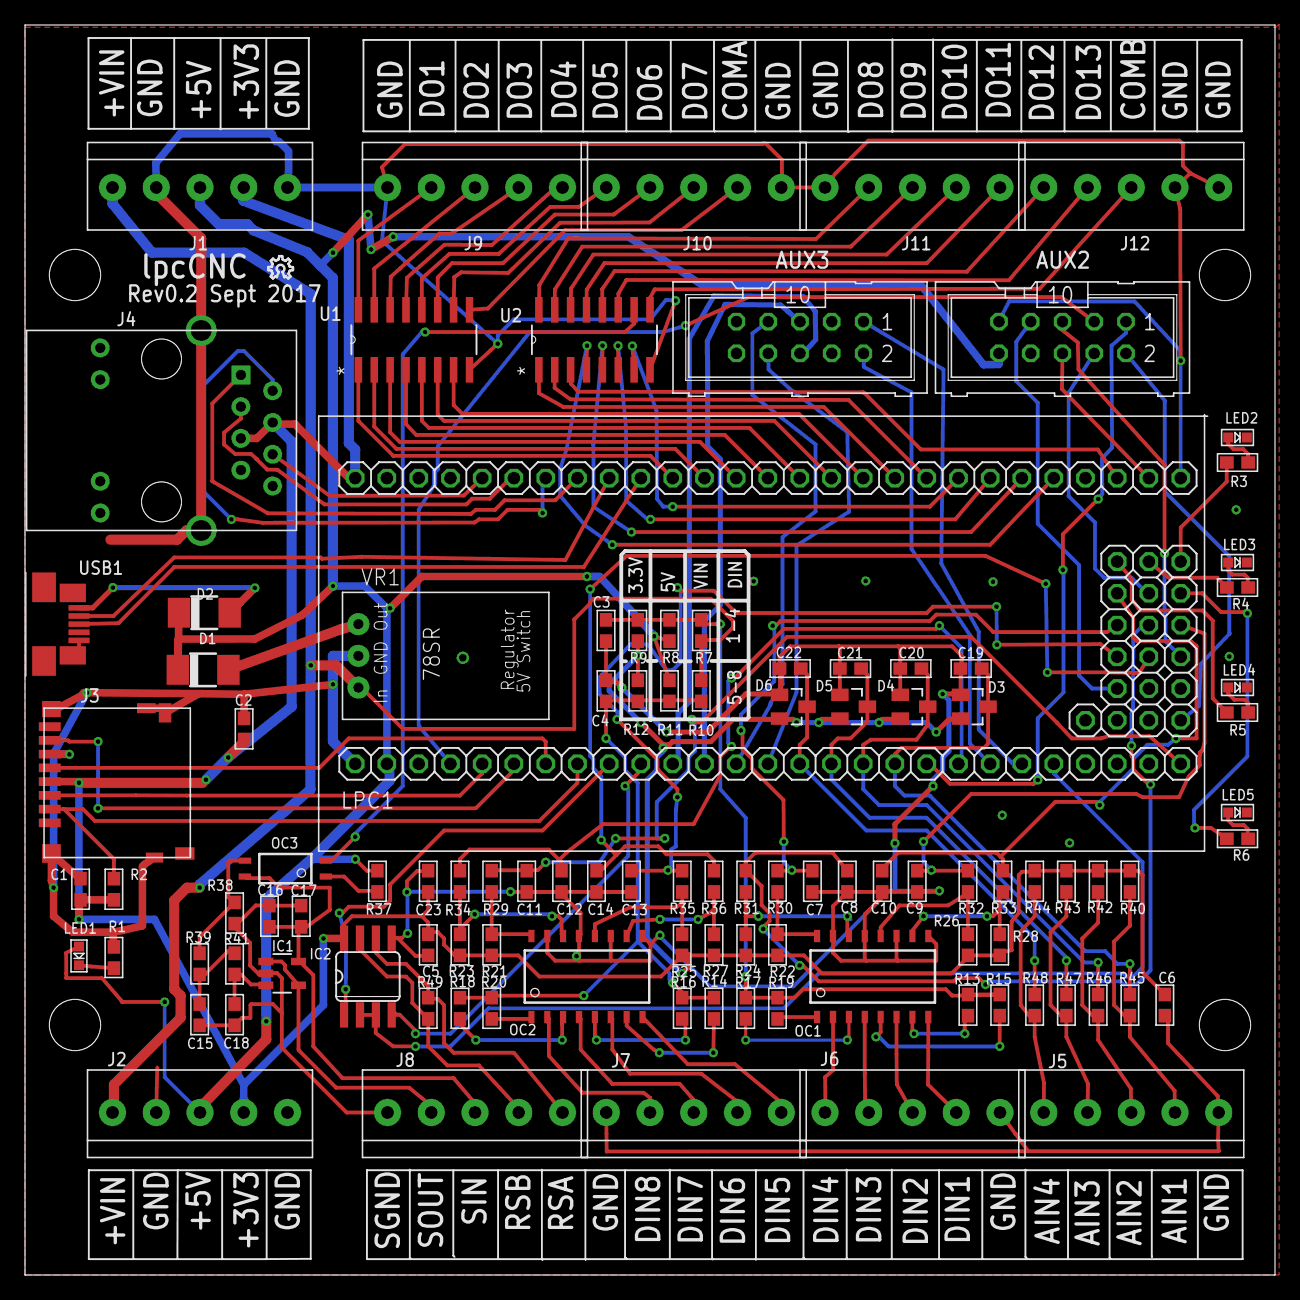
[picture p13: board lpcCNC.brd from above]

Board: 2 copper layers, 100.0 x 100.0 mm, 108 parts (0 on the bottom side), 122 nets.

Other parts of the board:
U$1: OSHW_8X70_NOTEXT

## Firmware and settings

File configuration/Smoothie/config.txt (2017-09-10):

# lpcCNC configuration file, 
# NOTE Lines must not exceed 132 characters, and '#' characters mean what follows is ignored


## Robot module configurations : general handling of movement G-codes and slicing into moves

grbl_mode    true

# Basic motion configuration
default_feed_rate                            1000             # Default speed (mm/minute) for G1/G2/G3 moves
default_seek_rate                            2000             # Default speed (mm/minute) for G0 moves
mm_per_arc_segment                           0.0              # Fixed length for line segments that divide arcs, 0 to disable
#mm_per_line_segment                         5                # Cut lines into segments this size
mm_max_arc_error                             0.01             # The maximum error for line segments that divide arcs 0 to disable
                                                              # note it is invalid for both the above be 0


# Arm solution configuration : Cartesian robot. Translates mm positions into stepper positions
# See http://smoothieware.org/stepper-motor
alpha_steps_per_mm                           16.66666              # Steps per mm for alpha ( X ) stepper - was 80
beta_steps_per_mm                            16.66666              # Steps per mm for beta ( Y ) stepper - was 80
gamma_steps_per_mm                           666.6666              # Steps per mm for gamma ( Z ) stepper


# Planner module configuration : Look-ahead and acceleration configuration
# See http://smoothieware.org/motion-control
acceleration                                 200              # Acceleration in mm/second/second.
#z_acceleration                              500              # Acceleration for Z only moves in mm/s^2, 0 uses acceleration which is the default. DO NOT SET ON A DELTA
junction_deviation                           0.05             # See http://smoothieware.org/motion-control#junction-deviation
#z_junction_deviation                        0.0              # For Z only moves, -1 uses junction_deviation, zero disables junction_deviation on z moves DO NOT SET ON A DELTA

# setup the step pulse length to around 10us ( 8 is max value )

microseconds_per_step_pulse                  8

# Cartesian axis speed limits
x_axis_max_speed                             2000             # Maximum speed in mm/min
y_axis_max_speed                             2000             # Maximum speed in mm/min
z_axis_max_speed                             1000             # Maximum speed in mm/min

# Stepper module configuration 
# Pins are defined as  ports, and pin numbers, appending "!" to the number will invert a pin
# See http://smoothieware.org/pin-configuration and http://smoothieware.org/pinout
alpha_step_pin                               0.4              # (DO1) Pin for alpha stepper step signal
alpha_dir_pin                                0.5             # (DO2) Pin for alpha stepper direction, add '!' to reverse direction
alpha_en_pin                                 0.10             # (DO3) Pin for alpha enable pin
alpha_max_rate                               3000             # Maximum rate in mm/min

beta_step_pin                                0.11             # (DO4) Pin for beta stepper step signal
beta_dir_pin                                 2.0!             # (DO5) Pin for beta stepper direction, add '!' to reverse direction
beta_en_pin                                  2.1              # (DO6) Pin for beta enable
beta_max_rate                                3000             # Maxmimum rate in mm/min

gamma_step_pin                               2.2              # (DO7) Pin for gamma stepper step signal
gamma_dir_pin                                2.3             # (DO8) Pin for gamma stepper direction, add '!' to reverse direction
gamma_en_pin                                 2.4              # (DO9) Pin for gamma enable
gamma_max_rate                               300.0            # Maximum rate in mm/min


## Endstops
# See http://smoothieware.org/endstops
endstops_enable                              true             # The endstop module is enabled by default and can be disabled here
#corexy_homing                               false            # Set to true if homing on a hbot or corexy
alpha_min_endstop                            1.26            # (DIN4) Pin to read min endstop, add a ! to invert if endstop is NO connected to ground
#alpha_max_endstop                           1.25^            # Pin to read max endstop, uncomment this and comment the above if using max endstops
alpha_homing_direction                       home_to_min      # Or set to home_to_max and set alpha_max and uncomment the alpha_max_endstop
alpha_min                                    0                # This gets loaded as the current position after homing when home_to_min is set
alpha_max                                    200              # This gets loaded as the current position after homing when home_to_max is set
beta_min_endstop                             1.23            # (DIN1) Pin to read min endstop, add a ! to invert if endstop is NO connected to ground
#beta_max_endstop                            1.27^            # Pin to read max endstop, uncomment this and comment the above if using max endstops
beta_homing_direction                        home_to_min      # Or set to home_to_max and set alpha_max and uncomment the alpha_max_endstop
beta_min                                     0                # This gets loaded as the current position after homing when home_to_min is set
beta_max                                     200              # This gets loaded as the current position after homing when home_to_max is set
#gamma_min_endstop                           1.26            # (DIN3)Pin to read min endstop, add a ! to invert if endstop is NO connected to ground
gamma_max_endstop                            1.25            # (DIN3)Pin to read max endstop, uncomment this and comment the above if using max endstops
gamma_homing_direction                       home_to_max      # Or set to home_to_max and set alpha_max and uncomment the alpha_max_endstop
gamma_min                                    0                # This gets loaded as the current position after homing when home_to_min is set
gamma_max                                    200              # This gets loaded as the current position after homing when home_to_max is set

alpha_max_travel                             500              # Max travel in mm for alpha/X axis when homing
beta_max_travel                              500              # Max travel in mm for beta/Y axis when homing
gamma_max_travel                             500              # Max travel in mm for gamma/Z axis when homing

microseconds_per_step_pulse 				 8 

# Optional enable limit switches, actions will stop if any enabled limit switch is triggered
alpha_limit_enable                           true             # Set to true to enable X min and max limit switches
beta_limit_enable                            true             # Set to true to enable Y min and max limit switches
gamma_limit_enable                           true            # Set to true to enable Z min and max limit switches

# Endstops home at their fast feedrate first, then once the endstop is found they home again at their slow feedrate for accuracy
alpha_fast_homing_rate_mm_s                  500             # Alpha/X fast homing feedrate in mm/second
alpha_slow_homing_rate_mm_s                  20             # Alpha/X slow homing feedrate in mm/second
beta_fast_homing_rate_mm_s                   500             # Beta/Y  fast homing feedrate in mm/second
beta_slow_homing_rate_mm_s                   20             # Beta/Y  slow homing feedrate in mm/second
gamma_fast_homing_rate_mm_s                  500                # Gamma/Z fast homing feedrate in mm/second
gamma_slow_homing_rate_mm_s                  20                # Gamma/Z slow homing feedrate in mm/second

alpha_homing_retract_mm                      5                # Distance to retract from the endstop after it is hit for alpha/X
beta_homing_retract_mm                       5                # Distance to retract from the endstop after it is hit for beta/Y
gamma_homing_retract_mm                      5                # Distance to retract from the endstop after it is hit for gamma/Z
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

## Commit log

2017-09-07 Initial File Upload
    Add Eagle files
    [lpcCNC.brd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]
2017-09-07 Add files for case
    Fusion 360 archive and STL files
    [lpcCNC_Base v7.f3d, lpcCNC_Base v7.stl, lpcCNC_Lid v15.f3d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]
2017-09-10 Add Smoothie confog for Shapeoko and pin document
    [config.txt]

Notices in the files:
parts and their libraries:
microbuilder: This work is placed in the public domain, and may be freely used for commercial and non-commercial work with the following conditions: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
